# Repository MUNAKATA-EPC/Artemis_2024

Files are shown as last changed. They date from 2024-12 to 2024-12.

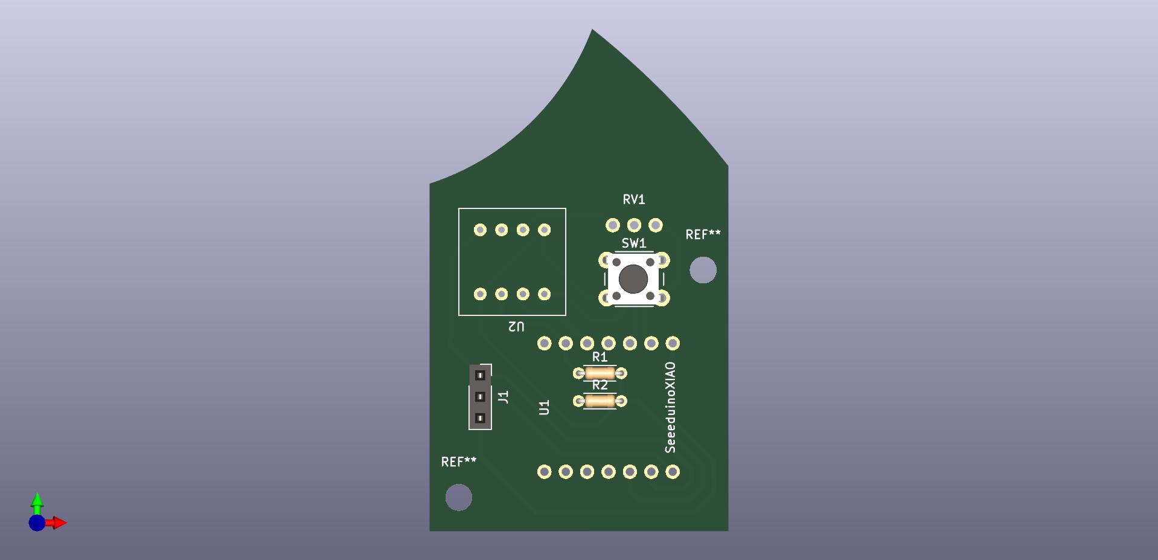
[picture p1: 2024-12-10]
Project_Testing_AkizukiMotor/Hardware/3d_data/gyro_board_texture/gyro_board.jpg

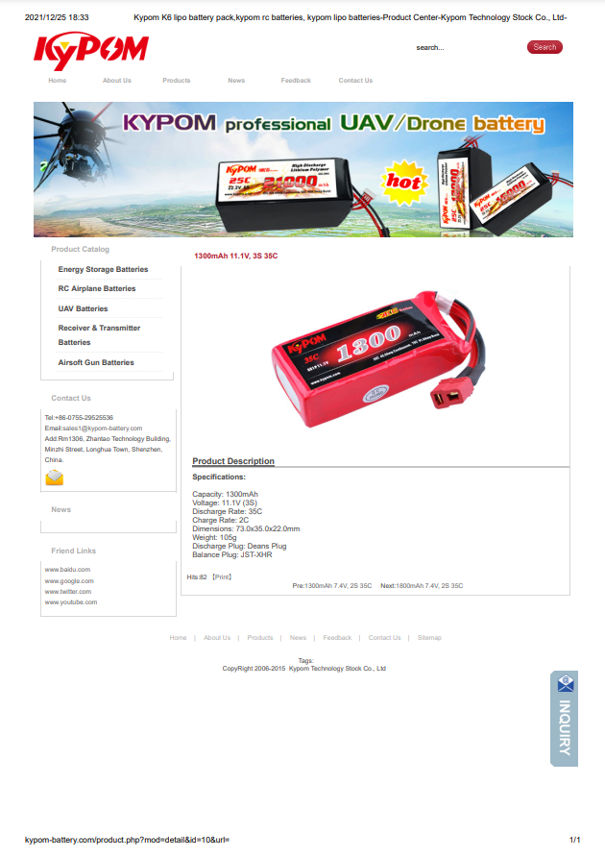
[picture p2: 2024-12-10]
CommonData/Tounaments_Data/2024_04_JapanOpen/battery_document/提出/WSL000_3.png

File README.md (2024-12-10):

# Artemis_2024

宗高アルテミス 2024シーズンリポジトリです。

OpenLeague→LightWeightと方針を転換しました。
OpenLeagueの残骸に関しては2025シーズンに向けての開発と思ってもらえればよきです。

## 最終活動結果
### 北九州ノード 
  優勝  
### 九州ブロック 
  準優勝 / 優秀プレゼンテーション賞  
### RoboCupJunior2024 JapanOpen Nagoya 
  世界大会推薦順位3位  
### RoboCup2024 Eindhoven 
  Individual 3rd Place / Top Poster & Presentation  

## リポジトリについて
・フォルダ階層をきれいにしよう  
・パス設定は相対パス基準にしよう  
・あとは動けばなんでもよし。  

## 命名規則など
・各ロボットごとにプロジェクトファイルを作成しましょう。(英字表記推奨、フォルダ名に2バイト文字は嫌じゃ！！！！)  
　ex. Project_FukuokaNode

・PlatformIO等で作成されたプロジェクトフォルダの名前は (プロジェクト名)-(開発環境) にしましょう。  
　ex. hogehoge-teensy40 hugahuga-seeeduinoxiaorp2040
 
・KiCad、Fusion360などで作成されたフォルダ、ファイルの名前は一目でわかる名前にしましょう。  
　間違ってもファイル名を"unko"とかにするなよ！！！！！(戒め)

 ## 使用ソフト
 |系統|ツール|
 |----|----|
 |ロボット設計|Autodesk Fusion 360  |
 |回路設計|KiCad 6.x (only use 6.x ver.)  |
 |プログラム開発|Microsoft Visual Studio Code <br>Arduino IDE   |

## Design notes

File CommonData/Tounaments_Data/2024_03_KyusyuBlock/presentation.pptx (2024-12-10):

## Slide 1

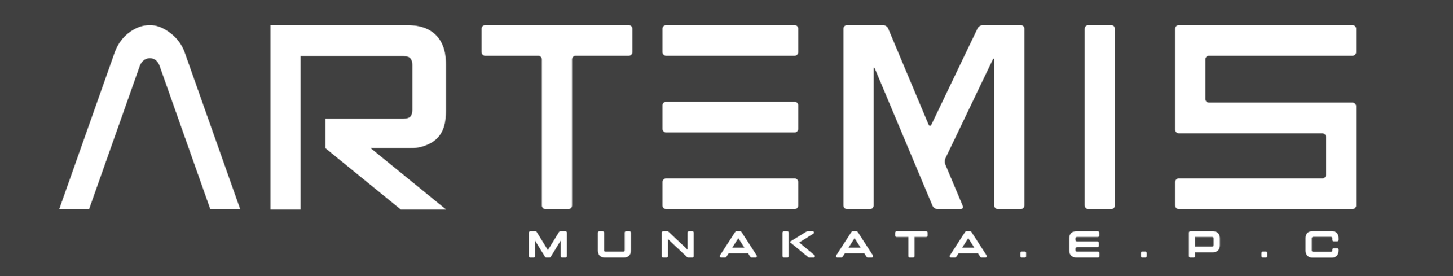
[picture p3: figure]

福岡県立宗像高等学校

チームメンバー

松田 魁琉 / 目野 優輝 / 石原 廉太郎 / 熊抱 崚太

所属ブロック

九州ブロック 北九州ノード

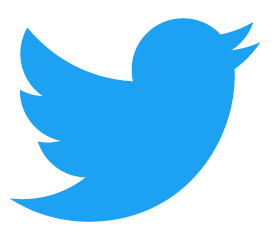
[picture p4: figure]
Twitterロゴのダウンロード方法と利用規約をわかりやすく解説

@munako_artemis

ロボットの概要 – 2024 Season Munako Artemis’ Robot

- 搭載している部品
・バッテリー　　　　:　KyPom 3Cell 1300mA
・モータードライバ　:　DSR-1202
・モーター　　　　　:　IG22 19:1 x 4
→ 応答性の高さから採用しました。
・メインマイコン　　:　Teensy 4.0 x 1
→ シリアル用ピンの多さから採用しました。
・サブマイコン　　　:　Seeeduino Xiao x 3
→ ジャイロセンサ・ラインセンサ・ボールセンサの処理用。
・ボールセンサ　　　:　TSSP58038 x 8
→ ボールから発せられる赤外線を読み取り、サブマイコンで
計算を行ってボールの角度を距離を算出しています。
・ラインセンサ　　　:　S4282-51 x 16
→ 光変調フォトICを使用し、白線の判別をしています。
ベクトルの考えを用いて白線の角度を算出しています。

私たちのロボットでは多くのセンサを円形に配置して使用しています。

カメラ
正確には「カメラに用いる全方位ミラー」が円形となっています。
カメラの上部に円錐状のミラーを設置することで、全方向のコート
の状況を正確に把握することができます。
私たちのチームでは、敵ゴール、自ゴールの二つを色認識で取得し、
三角関数などを用いて角度・距離を算出しています。
これらのデータで、ロボットが敵ゴールを向きながらキックしたり、
自ゴールに戻りキーパーとして動いたりすることが可能になります。
特に敵ゴールを向きながらのシュートは強力で、中立点からのボール
も正確にシュートすることができます。

カメラ
搭載後…

カメラでゴールの角度を計算することで
ゴールに向かってシュートすることができる

何もないと入らないこのシュートも…

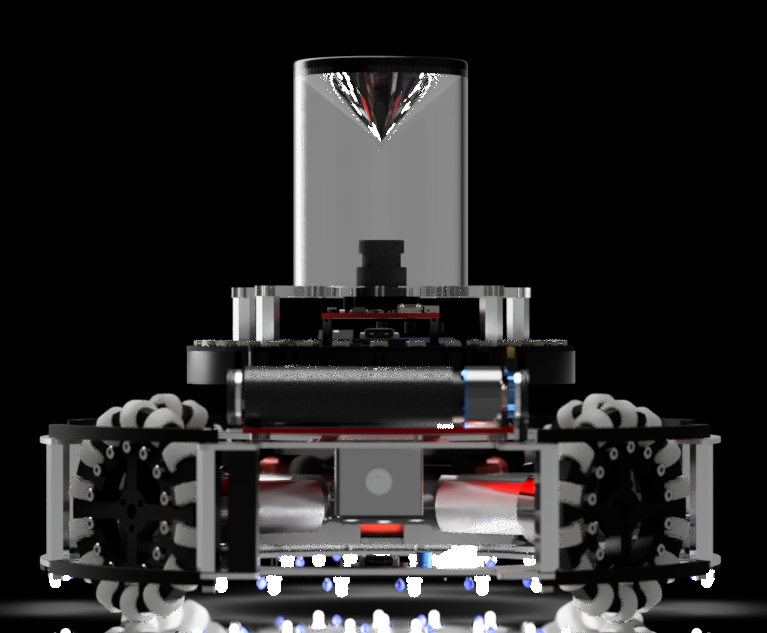
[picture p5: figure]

・ジャイロセンサ　　:　L3GD20H x 1
→ 主にロボットの姿勢を制御するために用いています。
・カメラ　　　　　　:　OpenMV H7 x 1
→ カメラ導入コストの低さから採用しました。
今回の機体では全方位ミラーを用いて360度の方向を監視しています。
・昇圧回路　　　　　:　XL6009
→ ソレノイド駆動電源の生成で使用しています。(12V → 30V)
・ソレノイド　　　　:　CB1037
→ 所謂「キッカー」という機構で用いています。
ボールをキックし推進力を与えることができます。
・ドリブラー用BLDC
→ AliExpressで購入した比較的小さいBLDCです。
ボールを自ロボット側に回転させることでボールを保持します。
主に安定したキックをするために使用しています。

金属製でロボットを強固に

- CNCによる金属加工 -

モーターの変更によりタイヤを強固に
固定する必要がありました。初めは3Dプリンタ
を用いて製作していましたが、部品が折れる
などの問題が頻発したため、OriginalMind社の
CNCを用いることで、時間のかかる金属加工を
自動で行い、タイヤ・タイヤ固定具を強固に、
そして安定させることができました。
(右図：ロボットに取り付けた金属部品)

ドリブルとキックで「魅」せる

- ドリブラーとキッカーの搭載 -

2024シーズンの私たちの新しい取り組みとして、「ドリブラー」「キッカー」の
搭載を行いました。ドリブラーは主にボールの保持、キッカーはボールのキック
という役割を果たします。
キッカー
キッカーの仕様は右図の通りです。
バッテリーからのの11.1Vを昇圧回路で
30Vに昇圧しています。また、
コンデンサへの充電部分、ソレノイド
駆動部分をFETによって分断することで
マイコンへのノイズ対策をしています。
Digital(黄色部分)はメインマイコンに
接続されており、フォトカプラに3.3Vの
電圧をかけることでそれぞれの信号を
出力させています。
キッカーによりゴール前における
プッシング発生率を大幅に減少させる
ことができます。
ドリブラー
ドリブラーにはAliExpressで購入したBLDCを用いています。3Dプリンタで制作した
回転体にゴムチューブを取り付け、それをBLDCを用いて回転させています。
そのままだとドリブラーがボールの高さより上に上がってしまい、ボールをうまく
回転させることができなかったため、回転部分と固定部分にバネの両端を
取り付けました。そうすることによって、
回転部分が回転した時にバネが捻られ、
元に戻そうとする力が働くことで結果的に
ドリブラーがボールをを押さえつける
という機構を実装することができました。
今大会では、ドリブラーを用いて、
ボールをゴールまで運んだり、
キックを安定させるための機構として
使用しています。

円形で全方位を見る

- 円形配置による全方位の監視 -

昇圧回路
12V → 30V

C
4700
μF

+30V

Digital

フォトカプラ

+30V

Pch MOSFET

フォトカプラ

ソレノイド

ボールセンサ
ボールセンサ(TSSP58038)を円形状に8個配置しています。ボールの角度・距離を取得するために、まずは一番反応している
センサーを取得し、次にその周囲3つのセンサーのデータを元に
ベクトル計算を行うことで、360度単位での角度取得が可能になりました。

ラインセンサ
光変調フォトIC(S4282-51)を円形に16個
配置し、2個ずつに分割してサブマイコンで
処理をしています。各センサーの値を見て
白線の角度を算出し、前回の白線の角度と
照らし合わせることで、「ロボットが白線を
踏んでいる」「ロボットが白線を超えた」
という状況を判別することができるように
なりました。

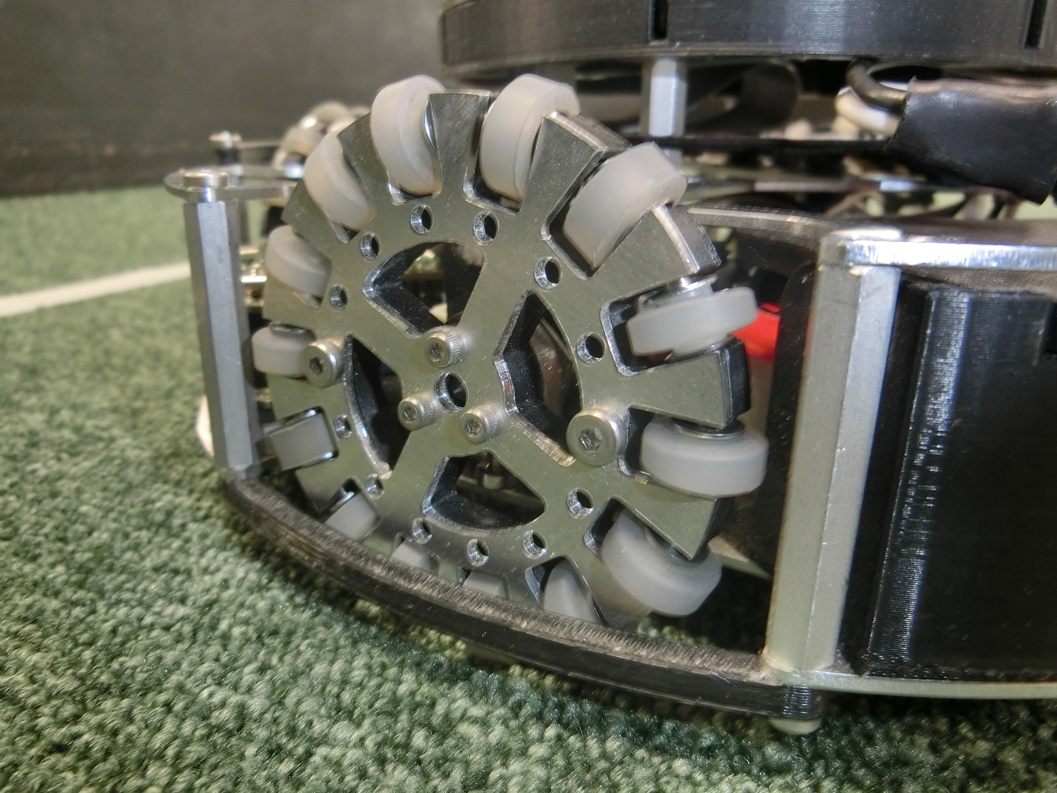
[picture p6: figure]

+30V

Nch MOSFET

+30V

+5V

Digital

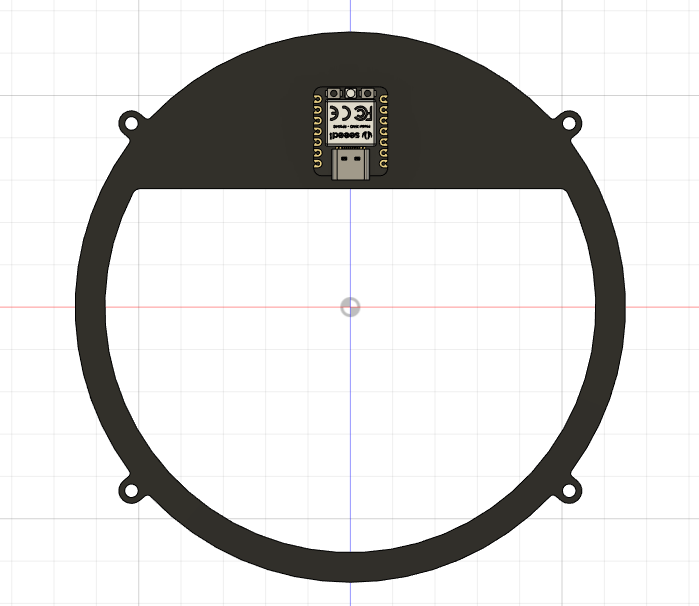
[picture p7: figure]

強いロボットは環境から

- 私たちの開発環境 -

私たちはロボットの開発のために以下のツールを使用しています。
環境を統一して活動することでロボットの開発を円滑に進めることができます。

<ハード>
ロボット設計　： Fusion360
基板設計　　　： KiCad 6.0
<ソフト>
プログラム制作：Visual Studio Code
Arduino IDE

<データ共有>
Githubを用いてチーム内で
リアルタイム共有を行っています。
<コミュニケーション>
Discord、Asanaを用いてタスクや進捗をチーム内で共有しています。

スポンサー

+30V

昨年度から白線外の空間が縮小し、白線外に出ないような
工夫が必要になりました。すべての速度を落とすという対策も
ありますが、これだと全体的なスピードを失うことになります。
そこで、ロボットの移動する角度を縦、横に分解し、その方向に
どのくらいの時間移動したかをタイマーで取得することで、
速度の変化の割合を変化させるという処理を実装しました。
これによって、コート内では素早く動き、白線付近では比較的
スローな移動にすることができました。

白線外など言語道断

- プログラムによる速度調節 -

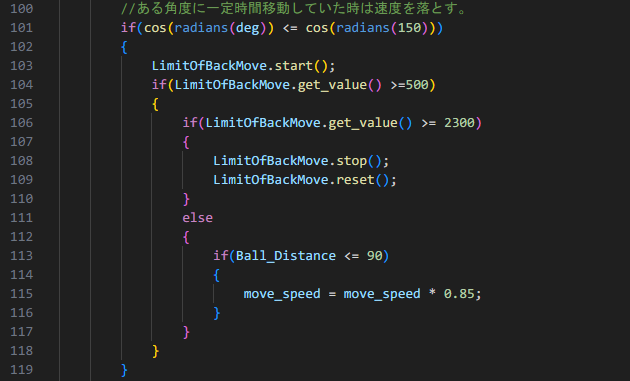
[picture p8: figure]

実際のプログラム
LimitOfBackMove というタイマー変数によってある方向に対する移動時間
の検知を行い、速度の割合を減少させている(115行目)。

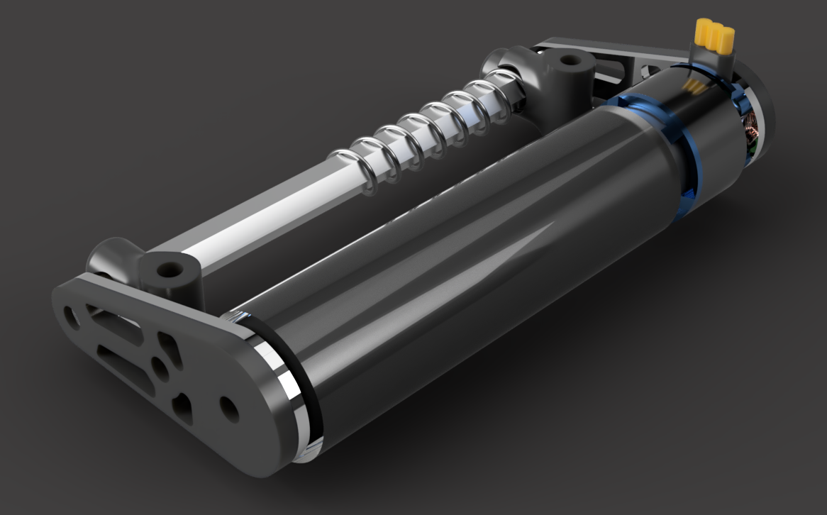
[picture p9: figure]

私たちが制作するロボットにはJLCPCB様の基板を使用しています。
JLCPCB様にスポンサーになっていただき、格安で基板製造をしていただいて
おります。また、JLCPCB様とのタイアップ記事も制作しているのでぜひ
JLCPCB及び私たちのウェブサイトをご覧ください。

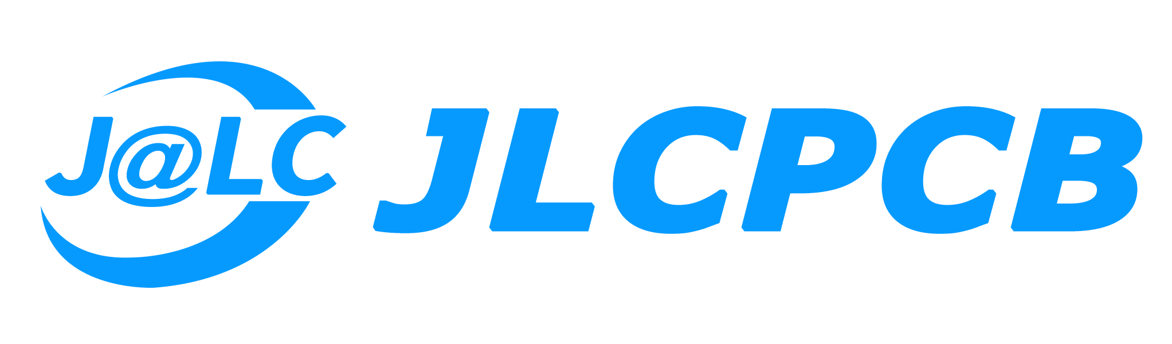
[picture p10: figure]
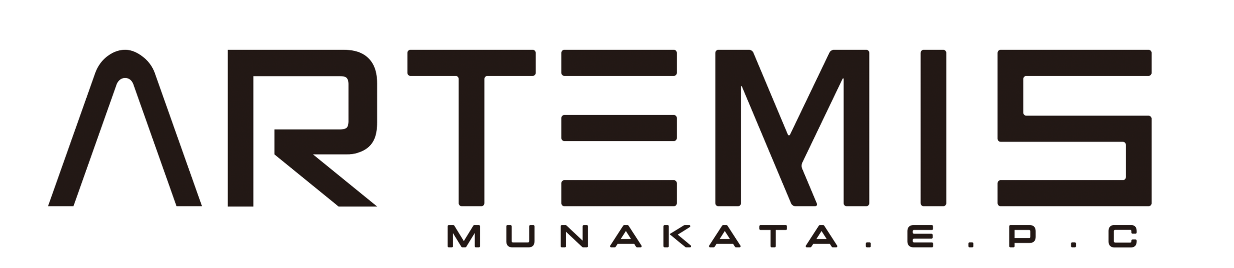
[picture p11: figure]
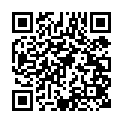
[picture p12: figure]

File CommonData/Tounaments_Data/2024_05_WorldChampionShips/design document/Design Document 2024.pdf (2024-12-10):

# Design Document 2024 Munako Artemis

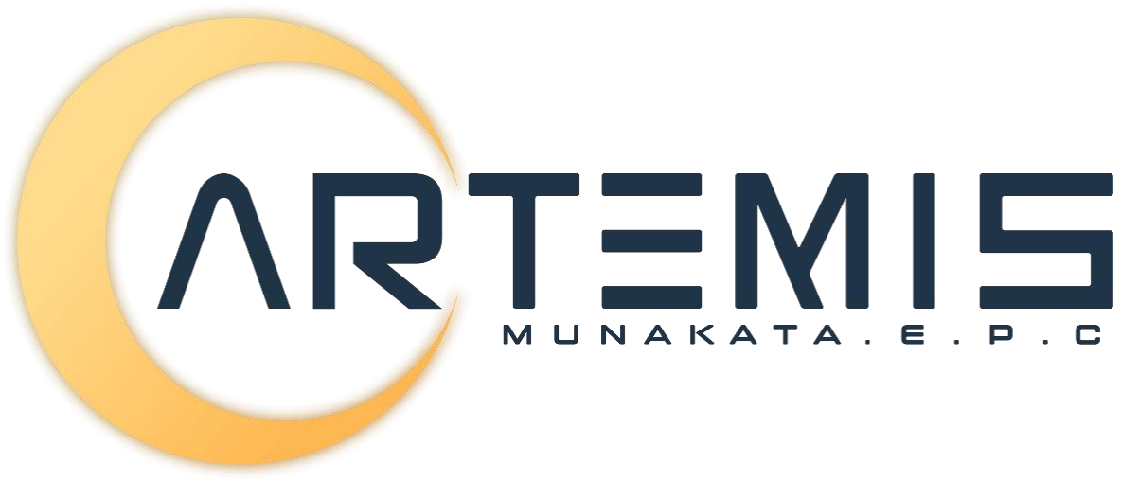
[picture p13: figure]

Munakata High School Electric Physics Club Region: Japan
League: Soccer Light Weight
Team member: Kyle Matsuda, Yuki Meno, Rentaro Ishihara, Ryota Kumadaki Team HP: https://munako-artemis.github.io/

### Team Introduction:

Munako Artemis is a Japanese team participating in Soccer LWL. The team consists of four high school students and has been active since 2021.

### Members:

・Kyle Matsuda | : Robot 1 Hardware (Robot design, Circuit design)
・Yuki Meno | : Robot 2 Hardware (Robot design, machining)
・Rentaro Ishihara: Robot 1 Software, Team management (Low layer programing) ・Ryota Kumadaki: Robot 2 Software (Main program)

### Abstract

| This year, we developed two types of robots. The robot in the
| left of fig.1 is designed to have a low center of gravity and high
| maintenance performance. The right one is designed to be a
| strong robot with stable operation. In the developments of
| these two robots, we made modifications to our robots to
| address various issues identified in the Japan Open 2024.
| We were given an extremely short preparation period for the
| world championship, so we proceeded with multiple workflows,
| which not only allowed us to start working on tasks earlier but
| also created significant time flexibility.

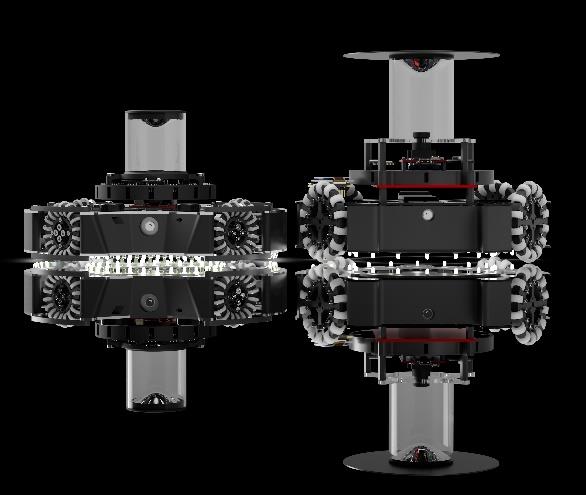
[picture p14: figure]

Fig.1 (robots for the world championship)

### Team Management

Our team is primarily divided into hardware and software teams. As a result, it was often difficult to understand the status of each team during actual activities. Additionally, the time available for work was limited due to the short period until the competition. Therefore, we made significant improvements in two main areas regarding our team activities.

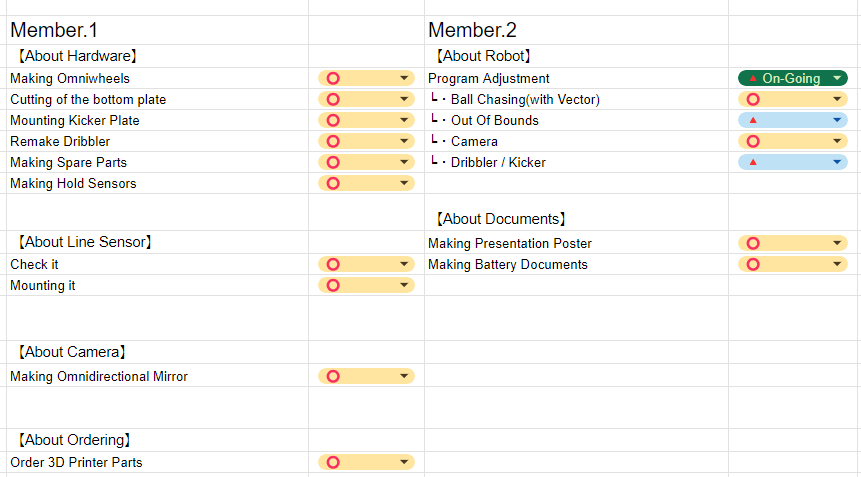
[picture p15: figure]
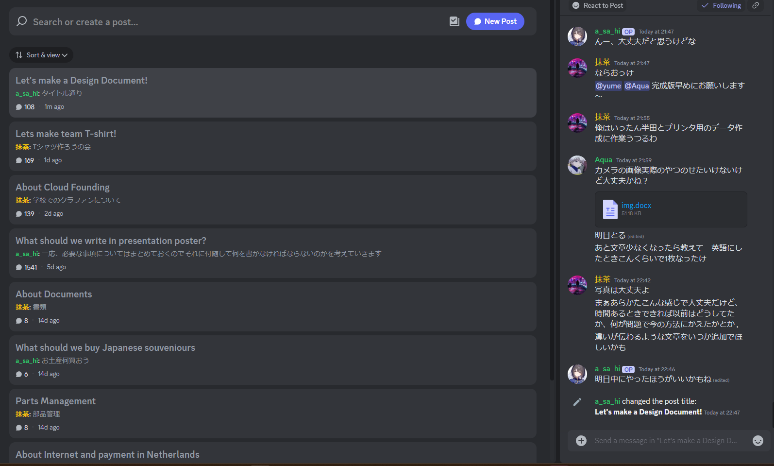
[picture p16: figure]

Fig.2 Task Management Tool (Google Spreadsheet) | Fig.3 Communication Tool (Discord)

<Task Visualization and Smooth Communication>
To visualize tasks, we used Google Spreadsheet. With Google Spreadsheet, we list and manage each team member's tasks (Fig.2). Since it can be used online, tasks can be checked at any time. Any team

member can add, delete, or edit tasks on the list, making it easy to reassign tasks to other team members if any issues arise. This allows the entire team to stay updated. This tool made task visualization clear and facilitated smooth team activities.
For smooth communication, we used Discord. Discord was primarily used for discussions related to team activities (Fig.3). By using the Discussion function, we could create channels for each topic,

enabling smooth discussions on specific topics.

<Workflow Improvement>
We had a short preparation period leading up to the world championship, necessitating efficient work processes. To address this, we focused on "improving our workflow."

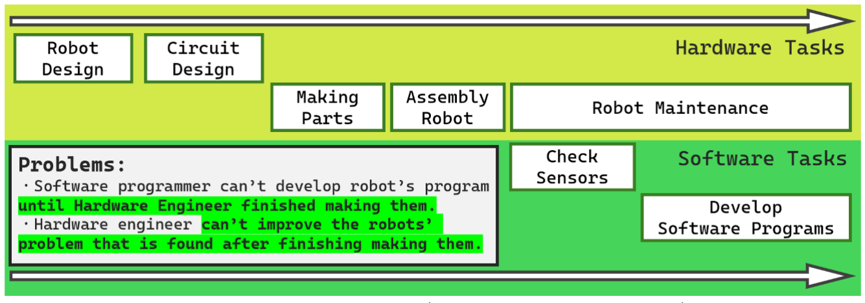
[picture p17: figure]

Fig.4 Single Workflow System (From Our Presentation Poster)

Previously, as shown in Fig.4, we followed a workflow system where tasks were completed one at a time. This method ensured more reliable results, but it takes longer to process tasks sequentially. As a result, it made it difficult to provide feedback from software development issues to the hardware team

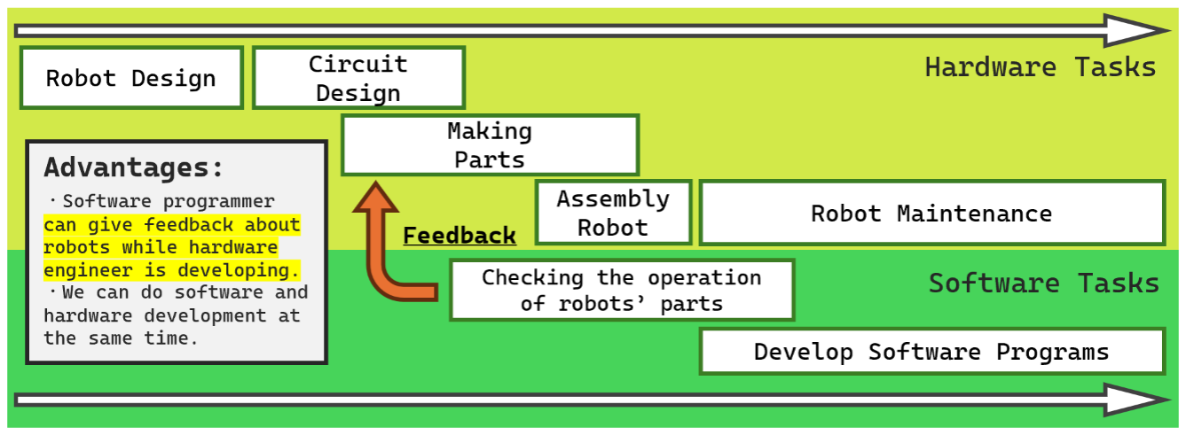
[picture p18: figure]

F ig.5 Multiple Workflow System (From Our Presentation Poster)

Therefore, we adopted a multitasking flow, as depicted in Fig.5, where team members work on multiple tasks in parallel. By working on tasks simultaneously, we enabled feedback from software to hardware, allowed system changes during the design phase, and confirmed the operation of each component before the robot's completion. This approach facilitated smoother program adjustments for the robot post-completion. By implementing these improvements in team activities, we were able to develop the robot smoothly and facilitate efficient team collaboration within a short period.

### Robot Specifics

<Robots’ Overview>

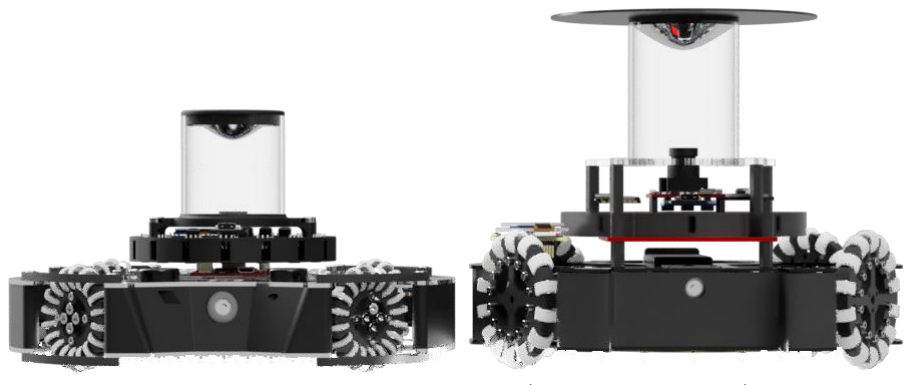
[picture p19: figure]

Fig.6 robots for the world championship (left: robot1 right: robot2)

Robot.1's concept is to be a "robot with a low center of gravity and high maintenance performance”. Also, it has been designed with a reduced number of components, ensuring ease of maintenance despite its low-profile design. Robot.2's concept is to be a "strong robot with stable operation". Additionally, it is designed to place various additional components for adapting to changes in rules.

<Robot1 Mechanical>
・low center of gravity

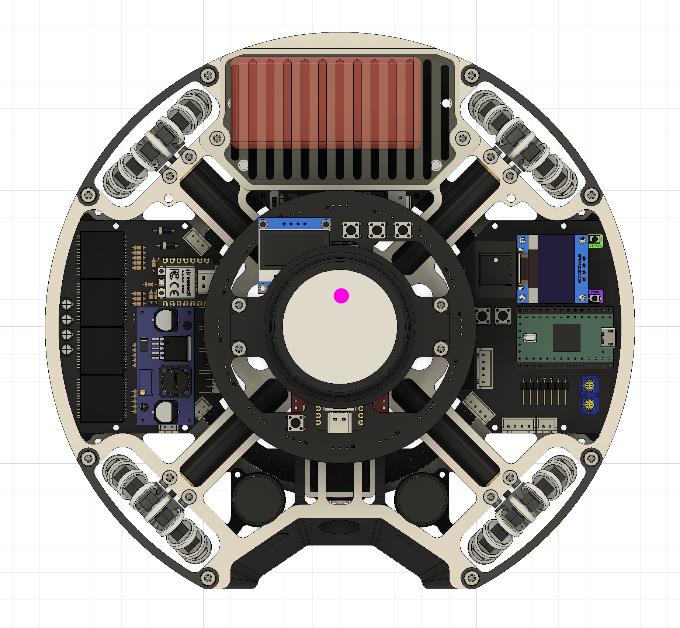
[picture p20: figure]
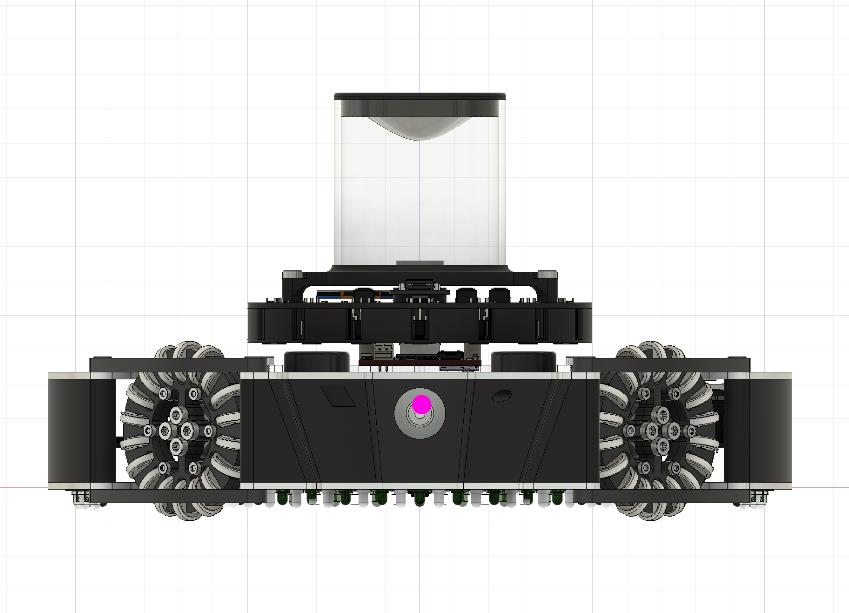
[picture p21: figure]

Fig.7 The position of the center of gravity of Robot 1.

This robot prioritizes a low center of gravity.
The pink dots shown in Fig.7 indicate the robot's center of gravity.
A low center of gravity allows the robot to execute turns and speed changes with minimal force, reducing power consumption and enabling more precise movements.
However, achieving a low center of gravity often means designing the robot to be compact and
densely packed with components internally, potentially compromising maintenance accessibility. To address this problem, we made various improvements shown on the next page to this robot.

・maintenance performance

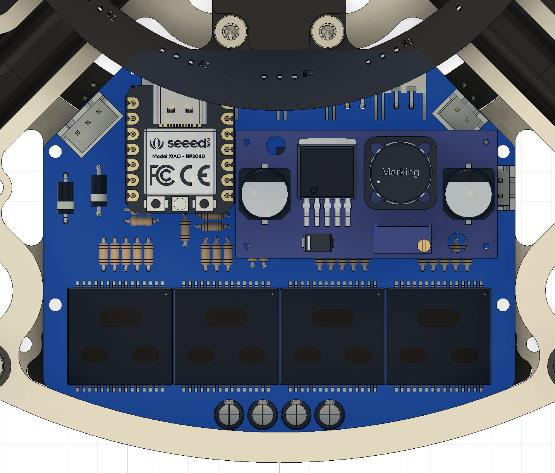
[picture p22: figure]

Fig.8 The shapes and location of some of the biggest boards in the robots. (Boards are colored in blue)

As mentioned earlier, low profile robots mean designing the robot to be densely packed with components internally, potentially compromising maintenance accessibility. Therefore, we paid special attention to the location and shape of the circuit boards. As shown in Fig.8, larger boards are especially placed in areas without obstacles, and designed to be secured with no more than four screws. Regarding the shape, instead of forming boards that fit tightly along the frame and surrounding components, we adopted simple shapes that do not interfere with other parts during removal.

・Improving the Shape of the Omni-Wheel

To achieve more stable and efficient movement, we changed the shape of the omni-wheel.

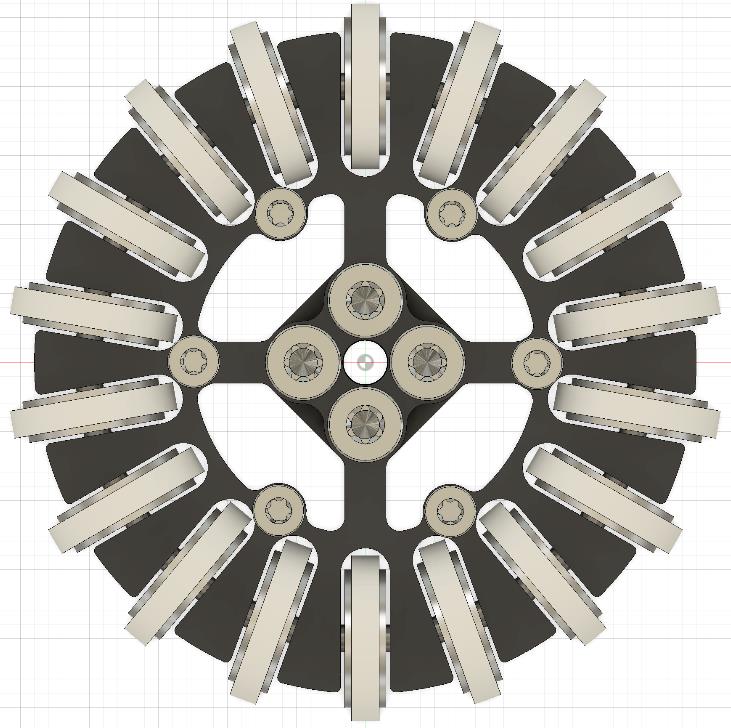
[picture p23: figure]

Fig.9 The old and new omni wheel

Previously, as shown in the left of Fig.9, we used omni-wheels with thick side wheels. However, starting from the 2023 Japan Open, we switched to a design with thin side wheels, as shown in the right of the Fig.9.

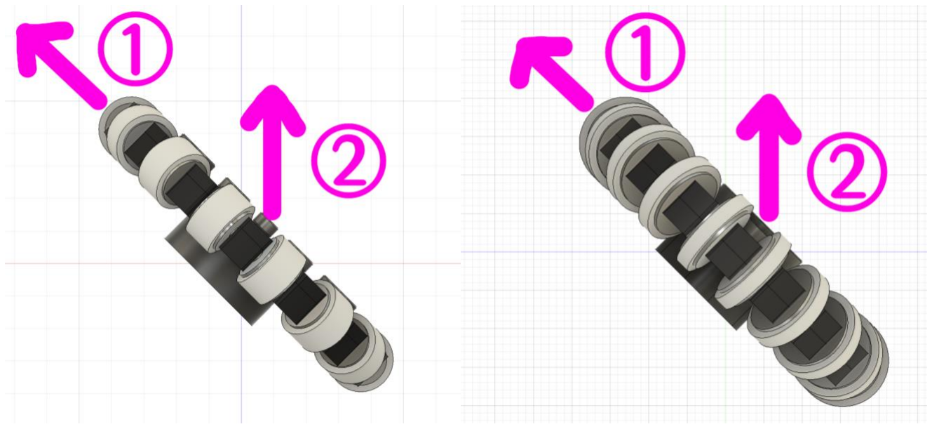
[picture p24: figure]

Fig.10

In the previous design, moving in direction →① was not a problem, but when moving in direction →②, the large contact area with the ground required more force due to increased friction. In the

current design, the thin side wheels reduce the contact area with the ground, resulting in less friction and allowing for easier movement with less force. Additionally, the difference in the amount of force needed depending on the direction is minimized, leading to less speed variation and more stable robot movement.

<Robot2 Mechanical>
・Designing

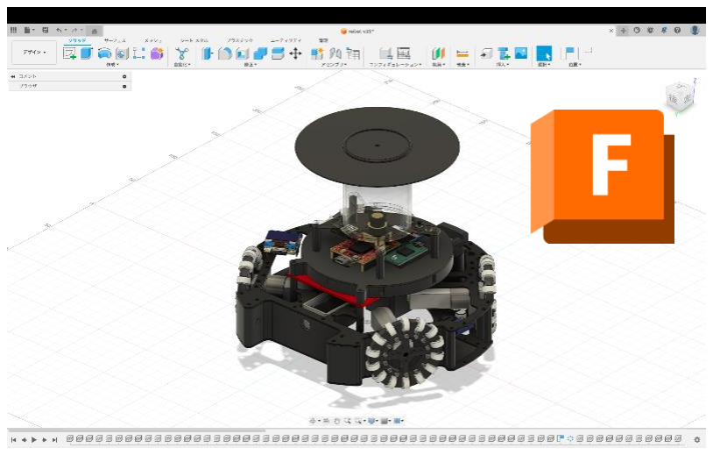
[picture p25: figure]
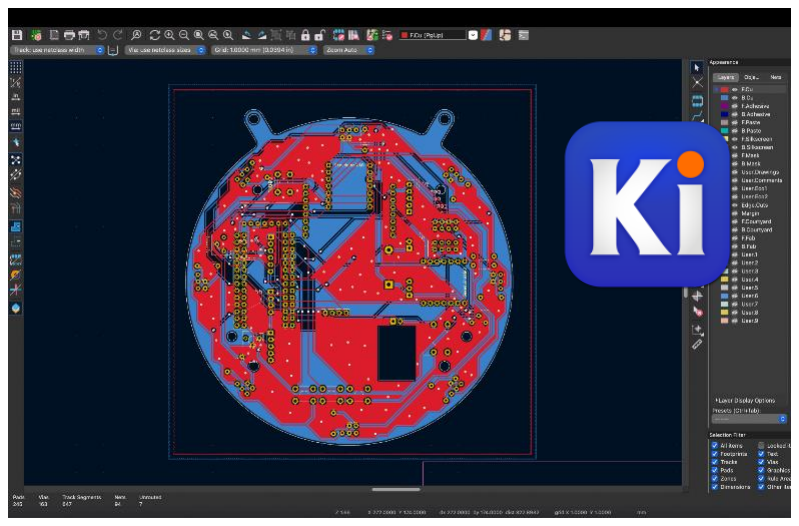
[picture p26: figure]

Fig.11 | Fig.12

We use Autodesk Fusion for the design of Robot 2 and KiCad 6.0 for the circuit design. By using these software tools, we have been able to develop a high-performance robot.

・Expansion Of The Ball Capture Zone

The robots we developed and produced up until the Japan Open 2023 had a narrow ball capture area, making it difficult to move the ball forward effectively and capture it smoothly during matches. (fig.13)

For the robots developed for the world competition, we have expanded the ball capture area compared to the previous robots. (fig.14) This expansion has resolved the issues faced by the earlier robots,

significantly improving the ball capture rate.


fig.13 | fig.14

・Improvement Of The Line Sensor

Until the Japan Open 2024, our robots were equipped with only circular line sensors. However, with only the circular line sensors, it was challenging to fully detect the white lines, leading to frequent out-of-bounds occurrence.
This time, as shown in the figure, we added side line sensors in addition to the circular ones.
This addition has significantly reduced the out-of-bounds rate compared to before.

・Motor Specifications

We use the DIGILENT IG22 1/19 motor. This motor is lightweight and compact yet offers high responsiveness and speed, which is why we chose it. Previously, we used motors with high torque and high rotation speed but lacked responsiveness, making posture control and sudden direction changes difficult, and programming the robot was extremely challenging. From this iteration, we have started using motors that combine high responsiveness.

・Solenoid Specifications

We use the TAKAHA solenoid for the kicker.
Specifically, we have chosen the CB1037 push solenoid from TAKAHA, which has a long stroke and delivers high output despite its small size. The kicker circuit is explained in detail on the next page under the section <Electric Circuits>.


### <Electric Circuits>

Our robots consist of two types, but we try to use the same circuits as much as possible to quickly determine the cause in the event of a failure and to make parts redundant.
In this document, we wrote about our power supply circuit and kicker circuit.

・Power Supply Circuit


Fig.15 (circuit of the power supply) | fig.16 (the circuit board)

The power circuit board includes a battery protection, and circuits for generating both the drive power supply and control power supply. The battery protection circuit is equipped with a reverse connection, overcurrent, and over-discharge prevention. To generate the control power supply, a DC-DC converter is used. By using a DCDC converter, electrical noise caused by motors and voltage drops due to the use of a kicker can be blocked, and a constant, stable power supply for control can always be provided. This ensures stable operation of the robot without resetting the microcontroller or sensors, even when equipped with high power motors or power-consuming dribbler mechanisms.

・Kicker Circuit


Fig.17 (circuit of the kicker circuit while charging) Fig.18 (circuit of the kicker circuit while kicking)

Previously, we did not implement noise countermeasures, resulting in voltage drops and unstable supply to the control power. This time, we have made numerous improvements to the kicker circuit to minimize noise as much as possible.
Firstly, to prevent noise from directly affecting the microcontroller, we have introduced a photocoupler into the signal lines. Secondly, we use separate FETs for solenoid control and isolate the kicker circuit from all other circuits only at the moment of the kick. This approach not only prevents noise from directly reaching the control circuits but also eliminates noise transmission through the power supply, leading to a much more reliable kicker circuit.

### <Robot1’s Software>

・Processing of the Defense Program


Fig.19 Defender System

Robot.1 primarily serves as a defender. The defense system is implemented using two types of sensors: a circular line sensor and a ball sensor. The robot stays on the goal line and moves or stops based on the ball's angle of response. Fig.19 illustrates the defense system, where the large translucent circle represents the robot, and the smaller red and white circles within it represent the line sensors.
In Fig.19 (①), when the ball is detected within ±15° of the perpendicular angle formed by the line connecting the active line sensors, the robot stops. In Fig.19 (②), when the ball is detected beyond ±15° of the perpendicular angle, the robot moves in the direction indicated by the line sensor's angle towards the ball. Previously, the robot only moved in the direction of the ball while on the white line, which caused inefficiencies in returning to the goal line. By adjusting the movement direction based on the line sensor's response angle, the system now achieves two objectives simultaneously: staying on the goal line and moving towards the ball. This improvement allows for smoother movements and more effectively blocks the opponent's shots on goal.

・Line Sensor Algorithm


Fig.20 An algorithm of Circle Shape Line Sensor

Like Robot.2, Robot1 is equipped with a circular line sensor. By using a circular line sensor, the robot can accurately detect how it is crossing the white line, significantly improving the accuracy of out-of-bounds prevention.Fig.20 illustrates the algorithm of the sensor. In the figure, the right side of the white lines represents the inside of the court, while the left side represents the out-of-bounds zone. In cases ① and ②, the robot moves in the direction opposite to the sensors that detect the white line. In case ③, the detected direction would normally cause the robot to move towards the out-of-bounds

zone. However, by comparing the current angle of detection with the previous one, if there is a significant change, the robot recognizes that it has crossed more than halfway over the line. It then moves in the opposite direction to avoid going out of bounds. This way, the circular line sensor ensures the robot calculates the correct direction to move, even if it has crossed the line by more than half.

### <Robot2’s Software>

・Color tracking using a camera


Fig.21 360 view ＆ robot movement

Fig.21 shows an example of color tracking using OpenMV. By using an omni directional mirror, it is possible to see the entire court area at 360 degrees. In this example, thresholds for the colors of the goal and court are set as arc tangents, calculating angles and distances from the camera center simultaneously. The calculated angles and distances are transmitted via UART to the main microcontroller. Using the angles, the deviation between the goal's center direction and the robot is calculated, enabling PID control to orient towards the goal direction. This approach improves goal alignment rates compared to using only a gyro sensor. However, issues arose due to variations in lighting affecting how the goal appears. To address this, adjustments were made to the gamma value, contrast, and brightness of the images obtained from the camera, allowing the robot to adapt the visibility of the goal based on the current environment.
Regarding the Attacker mechanism, previously, the robot would orient towards the goal direction when the goal was visible and towards the front direction using the gyro sensor when the goal was not visible. However, a problem was identified at the national tournament where the visibility of the goal frequently alternated at the boundary of visibility, disrupting smooth movement as the direction control switched between gyro direction and goal direction. Therefore, a new approach was implemented where the robot faces the goal direction when holding the ball or when near the goal (as shown in Fig21). This change prevents frequent switching between goal and gyro directions, leading to an improved goal alignment rate.

### <Review ＆ Future Goals>

Our final goal is to achieve victory in both the Lightweight League and the Open League.
Reflecting on this season, we aim to develop an even better robot for the upcoming season based on the following lessons learned:
Improvements in Design: We aim to enhance performance by continuing to lighten the robot and strengthen its structure. Optimizing component placement and design shapes will further improve maintenance and durability.
Sensor and Control Systems: We plan to refine the accuracy and reliability of color tracking using cameras.
Enhancing Stability and Accuracy of Operations: Prioritizing responsiveness in gyro sensors and motors will enhance operational stability. Optimizing software algorithms will ensure flexibility in handling unforeseen situations.
Refinement of Competitive Strategies: Further refining the roles of attackers and defenders will allow for more strategic gameplay. We will consider additional features to support strategic play.
Team Coordination and Communication: Enhancing the use of project management tools will streamline team progress tracking and issue resolution. Improving communication among team members will foster better collaboration.
We are committed to developing a robot that is more advanced and competitive, building on the challenges and successes of this season.

### <URL>

・Our team HP: https://munako-artemis.github.io/・GitHub: https://github.com/MUNAKATA-EPC/ (https://github.com/MUNAKATA-EPC/Artemis_2023) ・Contact us: kyle.matsuda.0518@gmail.com

This document only covers a part of our robot.
If you have any other questions or concerns, please contact us.

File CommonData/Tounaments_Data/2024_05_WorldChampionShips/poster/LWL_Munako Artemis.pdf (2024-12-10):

# Robo.1

# Munako Artemis

# Munakata High School

# REGION

JAPAN | Soccer LWL

# LEAGUE

## Team Website

### https://munako-artemis.github.io/

## Team X(Twitter)

### https://x.com/munako_artemis

## Team GitHub

https://github.com/MUNAKATA-EPC | Website X(Twitter) | GitHub

# Team Member

Kyle Matsuda | : Hardware
Yuki Meno | : Hardware

## Rentaro Ishihara : Software Ryota Kumadaki : Software

### Munako Artemis is a Japanese team participating in Soccer LWL. The team consists of four

high school students and has been active since 2021.

For robot design, we mainly use Autodesk Fusion, and for circuit design, we use KiCad. By utilizing 3D printers and CNC milling machines, we efficiently created our robots. Almost all the sensors and microcontrollers are the same among both of our robots,

### simplifying parts management and increasing compatibility. Additionally, the programming

is primarily done in C+/ for most microcontrollers and in MicroPython for the camera.

In preparation for the world tournament, we made modifications to our robots to address various issues identified in the Japan Open 2024. One significant problem was the frequent occurrence of out-of-bounds, so we improved the shape of the line sensors from a linear to a circular design and changed the sensor processing algorithm. Additionally, we often had difficulty carrying the ball forward, so we expanded the ball-capturing zone to

make it easier to capture the ball and improved the ball-tracking algorithm.

Both of our robots are equipped with a kicker mechanism that uses a solenoid to kick the ball. However, we had no idea which voltage and capacitor capacity would result in the strongest kick. Therefore, we investigated how the kicking power changes with different voltages and capacitor capacities and created graphs to determine the optimal settings

for the strongest kick.

### Although this is our first time participating in a world tournament, we are strongly motivated by the desire to "interact with various people, acquire diverse knowledge, and gain valuable experiences." To share our knowledge with a wider audience, we have created

a website and social media accounts.

Robo.2 | Battery Kypom 3S 11.1V 1300mAh

### Motor

DIGILENT IG22 1/19

X 4

11.1V

11.1V

Motor Driver
DAISEN DSR-1202

IC:VNH2SP30 x 4
・0.3V ~ 16.0V
・15~30A / channel

11.1V

Voltage
Conversion Circuit

Using IC :
OKL-T/6-W12N-C
11.1V to 5.0V
5.0V
UART | ANALOG

11.1V

About
48V

### Kicker System

(Please look at
“Kicker System And
Research About
Voltage & Capacity Of
Capacitors”)

### Solenoid

CB1037 x 1

UART
I²C + Digital x 3

Debug System

O-LED
Display
SSD1306 x 1

Tactile Switch x 3
( For switching
robot’s mode)

I²C

UART

# Abstract

## 【About the kicking mechanism and the research about the voltage and the capacitance of capacitors】

Our robots are equipped with a solenoid which is used for a ball kicking mechanism. It can kick the ball when you apply high voltage to the solenoid and uses a big capacitance charging capacitor.
The circuit of the kicker mechanism is shown below Fig.1.

However, we had no idea how high the voltage and how big the capacitance of the capacitor should be when we use the solenoid as the kicking system.
Therefore, we decided to research how the kick power will change when we changed the voltage and capacitor capacitance.

## <Details Of Research>

Measure the difference of the kicking power when you changed the voltage applied to the solenoid and the capacitance of the capacitor to find the optimal conditions for equipping the solenoid on the robot.
This time we used capacitors from NIPPON CHEMI-CON, Nichicon, Rubycon.

## <Research Procedure>

Step 1. make a solenoid drive board which can change the charging capacitor and the voltage which will be applied to the capacitor.
Step 2. Measure the kick power (/1) by keeping the voltage constant and varying the capacitance of the capacitor.
Step 3. Measure the kick power (/1) by varying the voltage without changing the capacitance.
Step 4. Create a graph based on the experimental data obtained from Step 2 and 3.

(/1) Place a long ruler on the court and kick the ball on it and the kicking power is defined as the distance the ball stopped.

## <Results>

In Fig.2, you can see that the voltage variation and the change in kicking power follow a linear relationship. Similarly, in Fig.3, the change in capacitor capacity and the variation in kicking power also appear to follow a linear relationship.

## <Discussion>

Based on these findings, it is considered that higher voltage and larger capacitor capacity lead to greater kicking power. Therefore, we aimed to get as close as possible to the maximum voltage limit allowed by the rules, which is 48V, and selected capacitor capacities based on the available space inside the robot. Robo.1 was equipped with a ?/μF capacitor, and Robo.2 with two 4700μF capacitor, to maximize kicking power as much as possible.

# Our Robots’ Structure

# Method / Production / Design

# Data / Results / Discussion

Sub Controller

Seeeduino Xiao

Sub Controller

Seeeduino Xiao

# Team Activities

## 【Enhancing Team Collaboration with Various Tools】

### In our team, we make our collaboration in diverse aspects such as robot design and programming more efficient by using a variety of

tools.

### All the tools we use are shown below:

### ・Robot Design : Autodesk Fusion ・Circuit Design : KiCad 6.0 / 7.0

### ・Programming Tool : Visual Studio Code

### ・Source Management : GitHub

### ・Communication Tool : Discord

### ・Task Management : Google Spreadsheets

We have set up a team-specific server.
Threads are created for each content area to discuss various aspects in preparation for the world championship, making it easy to understand topics and discussions. (fig.5)
This allows team members to communicate smoothly online, leading to improved robotics
development. Fig.5 Our Discord Server

Fig.6 Task Lists
(From RCJ2024 JapanOpen)

We made a table summarizing tasks for each member. (Fig.6) By managing them online, all team members can add, delete, or edit tasks, simplifying task management within the team. Therefore, at any time, it's easy to understand who has what tasks and the current status of their progress.

## 【Enhancing Team Efficiency through Multiple Workflows】

In team development, the robot production and the software development is difficult to progress at the same time, and this often leads to a single workflow (Fig.7). Given the extremely short preparation period for the world championship, our team found that operating under a single workflow was highly inefficient. Therefore, we proceeded with multiple workflows (Fig.8), which not only allowed us to start working on tasks earlier but also created significant time flexibility.

Robot
Design

Circuit
Design
Making
Parts

Assembly
Robot

To achieve multiple workflows, as we mentioned earlier, we actively used task management tools and communication tools. This allowed the entire team to work on multiple tasks at the same time, thereby enhancing the efficiency of team activities.

### Hardware Tasks

Check
Sensors

Robot Maintenance

Develop
Software Programs

### Software Tasks

Fig.7 Specific System and Problems of Single Workflow

Fig.8 Specific System and Advantages of Multiple Workflow

### Hardware Tasks Robot Design

Circuit
Design
Making
Parts

Checking the operation
of robots’ parts

Assembly
Robot

Develop Software Programs

Feedback

Robot Maintenance

### Software Tasks

### Problems:

・Software programmer can’t develop robot’s program until Hardware Engineer finished making them. ・Hardware engineer can’t improve the robots’ problem that is found after finishing making them.

### Advantages:

・Software programmer
can give feedback about
robots while hardware
engineer is developing.
・We can do software and
hardware development at
the same time.

### Battery

Kypom 3S 11.1V
1300mAh

# 【Robots’ Features】

Gyro Sensors

L3GD20H
&
BNO055

### Vision System

Omnidirectional
Mirror OpenMV H7 x 1

11.1V Voltage Conversion
Circuit

Using IC :
OKL-T/6-W12N-C
11.1V to 5.0V
5.0V

11.1V

11.1V

### Motor

Maxon RE16

X 4

UART

DIGITAL

Sub Controller

Seeeduino Xiao

Line Sensors

S4282-51 x 22

IR Sensors

TSSP58038 x 16

UART

ANALOG

IR Sensors

TSSP58038 x 16

Sub Controller

Seeeduino Xiao
UART
ANALOG

Sub Controller

Seeeduino Xiao

I²C

Gyro Sensor

BNO055

Line Sensors

NJL7502L x 53

UART

### Vision System

Omnidirectional
Mirror OpenMV H7 x 1

I²C
Digital x 3

Debug System

O-LED
Display
SSD1306 x 1

Tactile Switch x 3
( For switching
robot’s mode)

### Main Controller

Teensy 4.0

Wireless
Communication

Twelite UART

Wireless
Communication

Twelite UART

### Main Controller

Teensy 4.0

### Solenoid

CB1037 x 1

### About 48V

Drive Circuit Board : Kicker System And Motor Driver

Sub Controller

RP2040 ZERO

Kicker System

(Please look at
“Kicker System And
Research About
Voltage & Capacity Of
Capacitors”)

Motor Driver

ｘ4
IC : VNH5019A-E

## 1 Omnidirectional vision system

We have positioned the camera facing upwards and placed an omnidirectional mirror at the top of an acrylic pipe.
By doing this, we can capture a 360-degree view from the robot without using multiple cameras, significantly simplifying control compared to using multiple cameras.
We are using OpenMV as camera module. It is programmed with MicroPython. It can be done color tracking easily and easy to handle.

## C. Main Board (Robot.2)

This board is equipped with a Teensy 4.0 as the main microcontroller, an L3GD20H and a BNO055 as IMU sensors, an OpenMV camera, an SSD1306 display, and TSSP58038 sensors for ball detection.
There are eight ir sensors installed to calculate the ball's angle using vector processing.
Two gyro sensors are installed to ensure redundancy in case one fails during the match.
Additionally, the display allows us to check the sensor values and to change the robot's mode without connecting it to a computer, making adjustments to the robot more easily.

## D. Motor Driver : DAISEN DSR-1202 (Robot.2)

We have adopted the DSR-1202 from the Japanese manufacturer DAISEN. It supports high current and can be easily used by connecting to the microcontroller via UART.

## E. Kicker Board (Robot.2)

We use the XL6009 voltage boost IC to step up the voltage to approximately 47V.
For noise reduction, during kicking, we utilize a P channel MOSFET to isolate the kicker circuit from all other circuits, effectively suppressing noise.
The circuit is equipped with two 50V 4700μF charging capacitors. ( For details, check the [ Data / Results / Discussion ] section )

## > Improvement of Ball Access Time through Ball Tracking Algorithm Enhancement

During the national competition, we identified the following issues with our ball tracking algorithm: Lack of distance-based control between the robot and the ball resulted in excessive rounding, leading to delayed ball access.

To address these issues, we developed the following ball tracking algorithm:

In the diagram on the right, we define Ball Angle as the angle of the ball relative to the robot, and Move Direction as the actual angle of movement of the robot.

A. When the robot is close to the ball (Fig.B-1)
Move in the tangential direction to the ball (= Ball Angle + 90) to approach the ball.
B. When the robot is far from the ball (Fig.B-2)
Add a constant (= Ball Angle + X) to move towards the ball.

By doing these, the robot can approach to it shorter way than before, and colliding with the ball is almost nothing, so own-goal was decreasing.

## - Improvement of the shape of the Line Sensor

During the Japan Open 2024, we identified the following issues with our line sensors:

・The sensors were located in the center of the robot.
→ It takes time for the sensors to detect the white line after the robot has crossed it.
・We can only control whether the entire sensor array has detected the line or not,
limiting our ability to implement out-of-bounds prevention measures effectively.
・Poor color compatibility between the sensors and the white line leads to erroneous detections.

To address these issues, we implemented the following improvements.

・Changing the type of the Sensor
Until now, we have been using a sensor called S4282-51. (Refer to the “Touch Sensor” diagram on the left for details.) Although it is resistant to external light, we encountered the issues mentioned earlier. Therefore, we have equipped one of the robot with a phototransistor (NJL7502S).
By changing the sensor, we can sufficiently detect the difference in response between white and green, enabling us to detect white lines and reduce occurrences of out-of-bounds. Additionally, we can adjust the threshold of response circuitry, allowing for more accurate detection of white lines.
(We decided to continue using the S4282-51 in the other robot to ensure redundancy in case the new line sensor encounters difficulties.)

・Changing the shape of the line sensor (Fig.A)
We added new sensors to the left, right, and rear in addition to the central circular line sensor. This allows the robot to immediately detect the white line when it crosses over it.

・Increasing the number of the sensor ports
For the circular line sensor, reading values from each sensor allows us to estimate the current position of the reacting white line.
This enables the robot to return to the court even when it crosses halfway over the white line.

# 【Robots’ Overview / Descriptions Of The Installed Parts 】

# SPONSERS

0

500

1000

1500

2000

15 | 20 | 25 | 30 | 35 | 40

## Kick Power vs. Voltage (Fig.3)

capacitance = 4700μF

(mm)

(V)

Ball Angle

90°

90°

90°

Move
Direction

Fig.B-1 ball-tracking system when ball is near

X°

Fig.B-2 ball-tracking system when ball is far

0

500

1000

1500

2000

2500

220 | 330 | 470 | 560 | 1000 | 2200 | 3300 | 4700

## Kick Power vs. Capacitance (Fig.2)

voltage = 22V

(mm)

(μF)

Autodesk
Fusion

KiCad GitHub

Discord

Google
Spreadsheet

## 2 Debugging components

We have placed menu operation buttons and a small LCD monitor at the rear of the robot.
These are positioned for easy access during a match, allowing us to check sensor values and change the robot’s
Mode without connecting to a computer.

## 8 Solenoid

We have selected Takaha's CB1037 solenoid for the kicker. Among solenoids of similar size in the series, it has a longer stroke and delivers greater kicking force relative to its size, making it ideal for a compact and high-power kicker unit.

## A. Main Board (Robot.1)

This board is equipped with the “Teensy 4.0” main microcontroller, the “BNO055” IMU sensor, the “Twelite UART” communication module for inter-robot communication, the tournament’s official communication module, and various control switches.
All of the data from microcontrollers and sensors on other boards is aggregated here, and this data is used to control the robot.

・Teensy 4.0: It has many serial ports and very high performance, making it suitable for high-precision control using many sensors and sub-microcontrollers.
・BNO055: It allows easy control and has less angular drift compared to other IMU sensors.
・Twelite: It enables easy communication by simply connecting it to the microcontroller via UART.

## 4 IR Sensor

We have chosen the TSSP58038 for the ball detection. By placing 16 of them in a circular pattern on the central board, we can calculate the angle of the ball more accurately.

## B. Drive Board (Robot.1)

This board incorporates a motor driver circuit and a kicker drive circuit.
We have chosen VNH5019 for the motor driver IC, and XL6009 for the voltage booster included to de kicker circuit.
The motor driver IC can handle a power supply voltage of up to 41V, which is more than three times the voltage supplied from the battery, and it supports an extremely high current of 30A, ensuring high durability.
The kicker circuit uses two types of MOSFETs, P-channel and N-channel. One is used for controlling the solenoid, and the other is used to disconnect the circuit during the kick motion.
By isolating the kicker circuit from other circuits during kicking, we can physically block the electrical noise caused by the voltage drop during the kicking motion and the back electromotive force generated when the solenoid's shaft returns. This ensures that no noise affects both the driving power supply and the control power supply.

## 6 Power circuit Board

The power circuit board includes battery protection circuits, and circuits for generating both the drive power supply and control power supply.
The battery protection circuits feature reverse connection protection, overcurrent protection, and over-discharge prevention.
To generate the control power supply, a DC-DC converter is used, which minimizes the electrical noise from the drive power supply, ensuring stable operation of the microcontrollers.

## 3 Ball Capture Detecting Sensor

We have placed an LED on one side of the ball supplement area, and an S4282-51 photodetector IC on the other side, which detects the ball supplement.
This IC responds only to light of a frequency synchronized with the IC itself, allowing it to be used even in daylight or under an indoor lighting without causing false detections, making it ideal for precise control.

## 5 Line Sensor

We have positioned a circular board in the center and a board with a circular cut-out shape on the outer edge.
Sensors placed on the outer edge enable immediate response to the line, and the sensors in the center ensures continuous line detection, even when the robot moves over the line.
The description about the line sensor is summarized in “Robot’s Feature” section.

## 7 Motor

Robot.1 : We use Maxon's RE16 series motors, which offer high efficiency and responsiveness, reducing the robot's power consumption and enabling finer movements.

Robot.2 : We have adopted the DIGILENT IG22 1/19 motor. Despite being lightweight, it offers high responsiveness and speed. Additionally, its affordability makes it an ideal choice for RoboCup soccer robots, which is why we adopted it.

## 9 Frame : A2017

The frame was designed using Autodesk Fusion and machined using a CNC. A2017 Duralumin, known for its excellent durability, allows for a lightweight yet extremely sturdy frame.

Robot.2's concept is to be a "strong robot with stable operation" for soccer competitions, which is a challenging feat to achieve. However, we have implemented various innovations to achieve this goal.
All components installed in Robot.2 have undergone a year-long development and testing process to ensure stability. Additionally, it is designed to place various additional components for adapting to changes in rules.
By completing the robot production process early and allowing sufficient time for adjustments, we can achieve stable operation and develop a "strong robot".

Fig.A a shape of line sensor

Fig.1. The circuit of the kicker mechanism

FET1 and FET2 are controlled by signals from the microcontroller. When FET1 is set to HIGH, the connected capacitors (C6, C7) will be charged up. When FET2 is set to HIGH, the solenoid
operates using the power stored in the charged capacitors. Setting FET1 to LOW isolates the kicker circuit from all other circuits using P channel MOSFET, effectively blocking electrical noise.

Robot.1's concept is to be a "robot with a low center of gravity and high maintenance performance". In a robot that moves freely around the court at high speed, having a low center of gravity is crucial. A low center of gravity allows the robot to execute turns and speed changes with minimal force, reducing power consumption and enabling more precise movements. However, achieving a low center of gravity often means designing the robot to be compact and densely packed with components internally, potentially compromising maintenance accessibility. To address this challenge, Robot.1 has been designed with a reduced number of components. Most parts and boards can be quickly removed and replaced, ensuring ease of maintenance despite its low-profile design.

Visual
Studio Code

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
# Robo.1

## Robo.1

## Robo.2

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
# Robo.2

3

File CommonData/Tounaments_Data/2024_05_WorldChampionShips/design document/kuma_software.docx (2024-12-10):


OpenMVによるカラートラッキング fig**(openmvideの画面)はOpenMVによる色とりの例である。全方認識可能なミラーを使用することにより、コート内を360度見ることが可能である。使用例としては、ゴールの色やコートの色の閾値をアークタンジェントとし、角度を計算し、同時にカメラ中心との距離を算出している。算出された角度と距離はシリアル通信でteensy（メインマイコン）に送られる。角度を用いて、ゴールの中心方向とロボットのずれを計算し、PID制御を行うことでゴール方向を向くことができる。ジャイロセンサーのみを用いたときよりもゴール率は高くなる。しかし、光の入り方によってゴールの見え方が変化する問題が起きた。その対策としてカメラから得られる画像のガンマ値、コントラスト、明度を変更した。これによってその場に応じてゴールの見え方を変えることができた。


アタッカー機について 以前はロボットが攻撃をするとき、ゴールが見えているときはゴール方向を向き、ゴールが見えていないときはジャイロセンサーを用いて前方向を向くようにしていた。 しかし、全国大会で問題が発覚した。それは、ゴールが見えるようになる境界でゴールが見えたり見えなかったりすることでジャイロセンサーでの方向制御とゴール方向での方向制御が頻繁に切り替わり、スムーズな動きができなかったことである。そのため、ボールを持った時、またはゴールに近くなったときにゴール方向を向く方法に変更した（fig上図）。これによってゴール方向とジャイロ方向の向きが頻繁に切り替わることを防ぐことができ、ゴール率をあげることが出来た。

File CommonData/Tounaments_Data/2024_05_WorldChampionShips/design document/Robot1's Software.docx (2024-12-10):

Robot1’s Software


- ディフェンスプログラムの処理

Fig.1 Defender System

Robot.1は主にディフェンダーの役割を果たします。

ディフェンスのシステムは、円形ラインセンサーとボールセンサーの2つを用いて実装しています。

ロボットはゴール前の白線の上にとどまり、ボールの反応角度によって移動・停止します。

Fig.1はディフェンスシステムを図示したもので、大きな丸(半透明)はロボット、その中にある小さな丸(赤や白)はラインセンサーを示しています。Fig.1 ① において、反応したラインセンサーを結ぶ線分の垂線の角度を基準として、ボールが垂線角度±15°であるときは停止します。

また、Fig.1 ② において、反応したセンサーを結ぶ線分の垂線角度±15°を超えたときは、ボールがある方向のラインセンサーの角度方向に移動します。

以前は、白線上で左右のうちボールのある方向にしか動かなかったため、ゴール前白線に戻る処理が実行されることで白線上の移動がスムーズに行われません。しかし、移動方向をラインセンサーの反応角度に変更することで、「ゴール前白線にとどまる」「ボール方向に移動する」の2つを同時に実現することができ、よりスムーズに相手からのボールのシュートを防ぐことができました。


- ラインセンサーのアルゴリズム

Fig.2 An algorithm of Circle Shape Line Sensor

Robot.2もそうですが、私たちのロボットには円形ラインセンサーが搭載されています。

円形ラインセンサーを用いることで、ロボットが白線をどのように踏んでいるのかが正確に検知できるため、アウトオブバウンズ対策の正確性向上に大きく役立ちます。

Fig.2は円形ラインセンサーのアルゴリズムについて図示したものです。図にある3つの白線において、右側がコート内、左側がアウトゾーンです。

①・②は、反応しているセンサーをもとに、反応したセンサーとは逆の方向に移動しています。

③では、反応しているセンサーを元にした移動方向はアウトゾーンに進む方向ですが、前回の反応角度と比較して、角度が大きく変化していたら「半分以上超えた」という風に検知することで、反応角度と逆に進みアウトオブバウンズを防いでいます。このように、円形ラインセンサーはロボットが半分以上ラインを越えても正しく移動方向を算出することができます。

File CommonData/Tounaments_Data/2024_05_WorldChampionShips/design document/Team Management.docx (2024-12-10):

Team Management

私たちのチームは、主にハードウェアチームとソフトウェアチームに分かれています。そのため、

実際のチーム活動において、どちらのチームが現在どのようなことをしているのかがわかりづらい状況が多くありました。また、大会までの期間が短く、確保できる作業時間が限られていました。

そこで、私たちはチーム活動について、大きく2つの点で改善をしました。

グラフィカル ユーザー インターフェイス, テキスト, アプリケーション

Fig.A Task Management Tool (Google Spreadsheet) Fig.B Communication Tool (Discord)

<タスクの可視化・コミュニケーションの円滑化>

タスクの可視化という面で、私たちはGoogle Spreadsheetというツールを使用しました。

Google Spreadsheetでは、主に各チームメンバーのタスクをリスト化・管理しています。(Fig.A) これはオンライン上で使用することができるため、どんな時でも各メンバーのタスクを確認できます。また、チームメンバーは誰でもタスクリストを追加・削除・編集することができるため、何か問題が生じた際も、タスクをほかのチームメンバーに渡したり、他のメンバーのタスクを受け持ったりすることが瞬時にでき、それをチームメンバー全員が確認することができます。

このツールによって、タスクを明確に可視化することができ、チーム活動をスムーズに行うことができました。

また、コミュニケーションの円滑化という面では、Discordというツールを用いました。

Discordでは、主にチーム活動における議論を行っています。(Fig.B) Discussion機能を使用することで、

トピックごとにチャンネルを作成することができ、1つのトピックについて円滑な議論をすることができます。

ssSS


<ワークフローの改善>


Fig.3 Single Workflow System (From Our Presentation Poster)

F ig.4 Multiple Workflow System (From Our Presentation Poster)

私たちは、世界大会までの準備期間が短く、作業を効率化する必要がありました。そこで、私たちは

「ワークフローの改善」を行いました。

今までは、Fig.1のように、タスクを1つずつこなしていくようなワークフローの体系をとっていました。

これは、全員が各タスクの確認を行うことで、より確実な成果を生むことができるというメリットが

ありますが、1つずつしかタスクを処理することができないため、時間がかかるというデメリットがあります。また、ソフトウェア開発において表面化した問題をハードウェアにフィードバックすることができないため、ロボットの改善がしにくいという問題があります。

そこで、Fig.2のように、各チームメンバーが並行して複数の作業を行う、マルチタスクフローという形をとりました。Fig.2で示しているのは多くのタスクの中から抜粋した一部のタスクですが、図のように

作業を並行して行うことで、ソフトウェアからハードウェアへのフィードバックが可能になり、設計段階でのシステム変更が可能になったほか、ロボットが完成する前に各部品の動作確認ができるため、

完成後のロボットのプログラム調整をスムーズに行うことができました。

以上のようなチーム活動の改善を行うことで、短い期間の中で、ロボットの開発をスムーズに行い、チーム活動を円滑に進めることができました。

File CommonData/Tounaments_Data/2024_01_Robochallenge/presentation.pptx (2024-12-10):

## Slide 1


チームメンバー

松田 魁琉 / 目野 優輝
石原 廉太郎 / 熊抱 崚太

所属ブロック

九州ブロック 北九州ノード

GitHub Logos and Usage · GitHub
白い背景に分離された丸い twitter ロゴ | プレミアムベクター

@munako_artemis


Artemis Homepage


ロボットの概要


2024シーズンから円形状のラインセンサを搭載しました。
今までは十字のラインセンサを用いていましたが、十字だと
一定の角度で反応しない場合が存在していましたが、
円形ラインセンサを搭載することでどの角度からでも一定の距離で必ず反応させることができるようになりました。

円形ラインを用いたライン制御

また、円形ラインを用いることで、ゴール前の白線を
ロボットが半分以上超えてしまった際にもコート内に
正確に戻ることができるようになりました。
これは、ラインセンサが反応した白線の角度を2ループ分記憶し、前回の角度を今回の角度のずれを比較することで実現
しています。

ロボットは左進行

コート内

左に反応が寄っているので右に動く

ロボットは左進行

コート内

右に反応が寄っているので左に動くが…？

前回との比較で「行き過ぎた」と判断して反応の寄り方と逆
方向に移動してアウトを防ぐ

十字ラインだと反応しない
角度が存在するが…

円形ラインにすることで
どの角度でも反応するように

ゴールへのアプローチ

私たちのロボットには全方位カメラを搭載しています。
コートを全方位見渡すことで、相手ゴールの認識を
行うことができ、ゴールの角度データを利用することで
ロボットがゴールの方向を向くことができ、常に前を向く
状態よりも圧倒的得点率を叩き出します。

デザインと機能性を兼ね備えたUI

私たちのロボットには、ロボットの
データを可視化・操作するためのUI
機構を搭載しています。具体的には、
ロボット後方部にLCDとしてSSD1306、
操作用のボタン・スイッチを計4つ
搭載しています。
LCDは、センサーのデータやロボットの現状、操作盤としての役割を果たしています。
スイッチを用いることで、ロボットのスタート・ストップ、画面の切り替え等を行えるようにしています。

- 搭載している部品
・バッテリー　　　　:　KyPom 3Cell 1300mA
・モータードライバ　:　DSR-1202
・モーター　　　　　:　IG22 19:1 x 4
→ 応答性の高さから採用しました。
・メインマイコン　　:　Teensy 4.0 x 1
→ シリアル用ピンの多さから採用しました。
・サブマイコン　　　:　Seeeduino Xiao x 3
→ ジャイロセンサ・ラインセンサ・ボールセンサの処理に使用。
・ボールセンサ　　　:　TSSP58038 x 8
→ ボールから発せられる赤外線を読み取り、サブマイコンで
計算を行ってボールの角度を距離を算出しています。
・ラインセンサ　　　:　S4282-51 x 16
→ 光変調フォトICと呼ばれるものを使用し、白線の判別をしています。
ベクトルの考えを用いて白線の角度を算出しています。
・ジャイロセンサ　　:　L3GD20H x 1
→ 主にロボットの姿勢を制御するために用いています。
・カメラ　　　　　　:　OpenMV H7 x 1
→ カメラ導入コストの低さから採用しました。
今回の機体では全方位ミラーを用いて360度の方向を監視しています。

ゴールを向くことでボールを入れることができる

これらがなければ、ロボットと
パソコンをケーブルで接続し、
わざわざデータを出力するという
工程を踏まなければなりません。
Uiはデザインとともに機能性を
兼ね備えた合理的な機構と言えます。


このままではゴールに
入れることはできないが…

ゴール

ゴール

ロボット製作は環境から

私たちのチームではロボット製作をより円滑に行うために様々なツールを用いています。これらのツールを用いることにより、
今まで時間がかかっていた作業等を大幅に削減することが
できるようになりました。

＜私たちが使用しているツール＞
・機体設計 : Fusion360
・基板設計 : KiCad 6.0
・ファイル・バージョン管理 : Github
・プログラム開発 : VSCode + PlatformIO(拡張機能)
・コミュニケーションツール : Discord, Asana

弊チームにはスポンサーが付いています。
スポンサーの方々のお陰で私たちのロボットが成り立っています、本当にありがとうございます。
・JLCPCB 様
基板発注時の金銭面の
サポートをして下さっています。

スポンサー

KiCad 5.1.10 Release - TALPKEYBOARD BLOG
GitHub を無料でダウンロード。2023 年最新版
Visual Studio Code - Wikipedia

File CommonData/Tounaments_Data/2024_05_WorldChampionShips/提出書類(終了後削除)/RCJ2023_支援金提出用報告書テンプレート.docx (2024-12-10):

リーグ | Soccer LightWeight | チーム名 | Munako Artemis
メンバー | 石原 廉太郎 / 松田 魁琉 / 目野 優輝 / 熊抱 崚太
所属ブロック | 九州ブロック | 所属 | 北九州ノード

大会参加の目的（目標）

・世界1位を獲る

・世界中のロボカップ参加者と交流し、様々な経験をする

大会の様子（会場の様子，試合の様子，チーム間交流の様子など）

・ロボカップシニアリーグ(SSL、中型リーグなど)がすぐそばに設置されており、会場的には端の方にL字で設置されていた。(パドックはLW/OPENで別)

・パドックは人数関係なく1つの机で、コンセントは共用。スペースは比較的狭めでゴチャゴチャしていた印象がある。

・全体的に緩めで、とにかく「大会に参加して楽しむ」を意識されていたような気がする。

・基本的にスコア管理の人がスコアをつける(iPad等での管理は無し)以外は基本的に全国大会と同じ。

・SuperTeamがとても盛り上がっていた。海外チーム間との交流もこの時に盛んに行った。

国内大会と違っていたと感じた点（良い点，悪い点）

<良い点>

・コミュニケーションモジュール

→ワンタッチでロボットのStop/Startができるという取り組みはとてもいいと思った。

・チーム間の交流のしやすさ

→パドックが基本隣接して隣同士で置いてあるため、チームの間での交流が必然的に

発生していた。

<悪い点>

・審判のルール熟知度

→ルールをよくわかっていないのか、コート端のライン(≠ゴール前白線)のところで

プッシングをとっていたり、過去のルールが適用されたままだったりの試合が

いくつか見受けられた。

また、ルールとは直接関係ないが、スコア管理が杜撰であった試合もあった。

・外野からの野次

→時々相手チームのメンター？からの野次が飛んでいた。

大会参加の成果（学んだこと，目標の達成度）

・アウトオブバウンズ対策の重要性

→基本的に「ロボットがずっとコート内にいるチームが強い」ため、白線から出ない

という当たり前のことを正確に行えるチームがとても強かった。

(特にEdge。ただ他のチームもラインから出ることは少なかった。)

・プッシング

→現状白線上にとどまりボールを受け止める(もしくはロボットとの押し合い)

ロボットがとても強い(=主にプッシングルールの存在)

ある程度の精度のキーパーであると、余程のことがない限りゴールには基本的に

入れることができなかった。(中国 UGAMM-SOCCER のキーパーは特に)

遠距離から斜めにキッカーで蹴り飛ばすなどの工夫が必要。

・目標について

→惜しくも世界大会優勝という目標をかなえることはできなかった。

しかし、1か月という短い準備期間の中で、総合3位・Top Poster & Presentation

という賞を持ち帰ることができたのはとても大きい。

また、海外のチーム(国内然り)からたくさん学べることがありとても面白かった。

大会参加を受けて日本のロボカッパーへのメッセージ

・日々の努力が大切

ロボットは一朝一夕でできるものではない。それはハードウェア然りソフトウェア然り。だからこそ、常日頃からロボットと向き合って努力することが大切。

世界大会で使った知識や経験は、基本的に日々の活動で身に着けた知識の応用がほとんど。実際に世界大会で強かったロボットは毎日調整していたのだなと感じるようなロボットだった。

・やっぱり世界大会は楽しかった

全国大会ももちろん楽しいが、世界大会はそれ以上に楽しかった。Super Teamやいろんな国の人との交流をし、ハプニングが起き、とにかくいろんなことが起きてとても楽しかった。全国大会を勝ち抜くことはそう容易ではない(私たちもギリギリ行くことができた)が、その先に待っているのはとても面白い光景だから、ぜひ世界大会に向けて活動を頑張ってほしいと思う。

・予備の準備

部品やマイコンの予備の準備はとても大切。だが、それ以上に、問題が発生したときにどう対処するかという準備がとても重要だった。

(準決勝前にモータードライバのマイコンが焼けた。原因特定に時間がかかり、準決勝中にロボットを修理することができなかった。)

成績（公式に残るものだけでなく予選の結果，交流戦などできるだけ詳しく）

・Round 1 vs. Oi_DENGIKEN（日本）●　５－６

・Round 2 vs. Andys Geese（カナダ）○　３１－０

・Round 3 vs. Bodensee-Luchse（ドイツ）○　２７－７

・Round 4 vs. RBL Stieren（メキシコ）○　１６－８

・Round 5 vs. UGAMM-SOCCER（マカオ）●　４－１２

・Round 6 vs. Righteousness（マカオ）△　８－８

・Round 7 vs. ETC autoPrikratki CRO Team（クロアチア）○　１３－４

・Round 8 vs. Edge（日本）○　１３－５

・Semi-Final　 vs. UGAMM-SOCCER（マカオ）●　１－１４

・3rd place play-off 　vs. Zenith（オーストラリア）○　２５－１　３位

会場，試合，対戦相手など記録となる写真（数枚）


その他

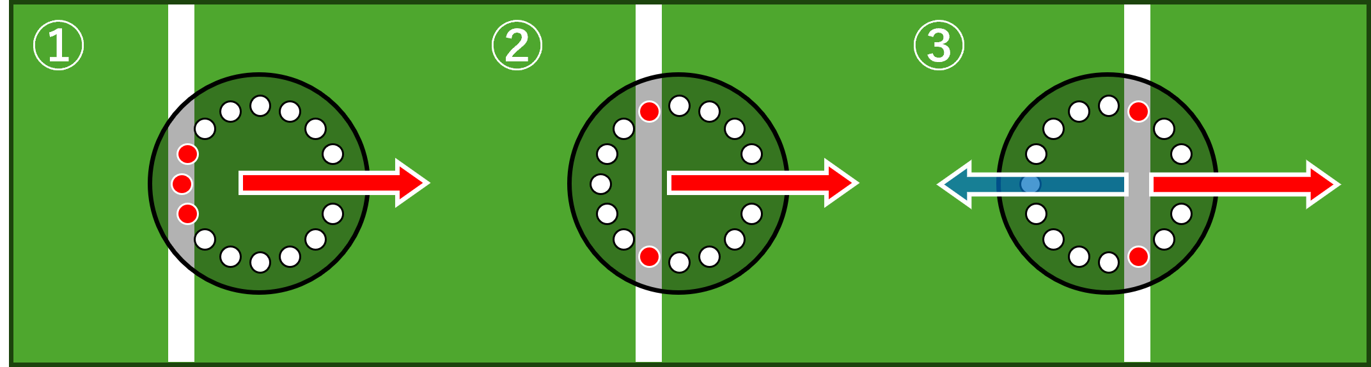
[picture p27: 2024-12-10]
CommonData/Tounaments_Data/2024_05_WorldChampionShips/design document/Engel Line Sensor.png

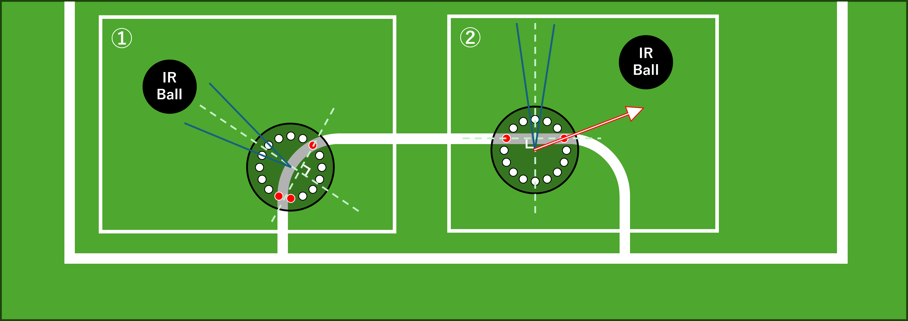
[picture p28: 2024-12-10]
CommonData/Tounaments_Data/2024_05_WorldChampionShips/design document/Defender.png

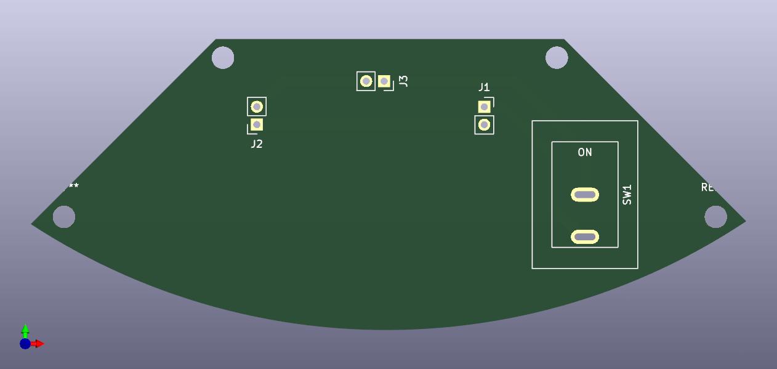
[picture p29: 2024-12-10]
Project_Testing_AkizukiMotor/Hardware/3d_data/supply_board_texture/supply_board.jpg

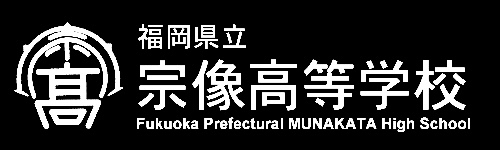
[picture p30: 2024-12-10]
Project_KOKUROU_dev.1/Others/ステッカー/up_ZL7NWUP5header_01.jpg

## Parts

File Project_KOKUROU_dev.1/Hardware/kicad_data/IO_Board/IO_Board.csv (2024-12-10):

Comment | Designator | Footprint | LCSC
WS2812B | D1,D2,D3 | LED_SMD:LED_WS2812B_PLCC4_5.0x5.0mm_P3.2mm | C2761795
Conn_01x08_Socket | J1 | Connector_PinHeader_2.54mm:PinHeader_1x08_P2.54mm_Vertical
SW_Push | SW1,SW2,SW3 | Button_Switch_THT:SW_PUSH-12mm_Wuerth-430476085716
SW_DIP_x01 | SW4 | Connector_JST:JST_XH_B2B-XH-A_1x02_P2.50mm_Vertical

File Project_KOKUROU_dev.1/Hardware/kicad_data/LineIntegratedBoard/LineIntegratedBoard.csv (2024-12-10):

Comment | Designator | Footprint | LCSC
Conn_01x08_Socket | J1,J2,J3 | Connector_PinHeader_1.27mm:PinHeader_1x08_P1.27mm_Vertical
Conn_01x05_Socket | J4 | Connector_PinHeader_1.27mm:PinHeader_1x05_P1.27mm_Vertical
CD74HC4067SM | U1 | Package_SO:SSOP-24_5.3x8.2mm_P0.65mm | C98457
SeeeduinoXIAO | U2 | Seeeduino_Xiao:Seeeduino XIAO-MOUDLE14P-2.54-21X17.8MM

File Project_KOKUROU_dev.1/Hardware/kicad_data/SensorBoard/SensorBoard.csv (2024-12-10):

Comment | Designator | Footprint | LCSC
SSD1306 | Brd1 | SSD1306:128x64OLED
C_Small | C1,C2,C3,C4,C5,C6,C7,C8,C9,C10,C11,C12,C13,C14,C15,C16 | Capacitor_SMD:C_0402_1005Metric
C | C17,C19 | Capacitor_SMD:CP_Elec_5x5.4
C | C18 | Capacitor_SMD:C_0402_1005Metric
WS2812B | D1,D2,D3,D4,D5,D6,D7,D8,D9,D10,D11,D12,D13,D14,D15,D16,D17,D18,D19,D20,D21,D22,D23,D24,D25,D26,D27,D28,D29,D30,D31,D32 | WS2812B:LED_WS2812B-Mini_3.5x3.5mm
Conn_01x10_Socket | J1 | Connector_IDC:IDC-Header_2x05_P2.54mm_Vertical
R_Small | R1,R2,R3,R4,R5,R6,R7,R8,R9,R10,R11,R12,R13,R14,R15,R16 | Capacitor_SMD:C_0402_1005Metric
SW_Push | SW1,SW2 | Button_Switch_THT:SW_PUSH_6mm_H5mm
CD74HC4067SM | U1 | Package_SO:SSOP-24_5.3x8.2mm_P0.65mm
SeeeduinoXIAO | U18 | Seeeduino_Xiao:seeeduinoXIAO
open_mv | U19 | OpenMV:OpenMV
TSSP58038 | U2,U3,U4,U5,U6,U7,U8,U9,U10,U11,U12,U13,U14,U15,U16,U17 | TSSP58038:TSSP58038
L7805 | U20 | Seeeduino_Xiao:3端子レギュレータ

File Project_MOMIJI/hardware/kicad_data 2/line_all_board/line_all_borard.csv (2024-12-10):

Comment | Designator | Footprint | LCSC
C_Small | C1,C2,C3,C4,C5,C6,C7,C8,C9,C10,C11,C12,C13,C14,C15,C16,C17,C18,C19,C20,C21,C22 | Capacitor_THT:C_Disc_D3.4mm_W2.1mm_P2.50mm
C_Small | C23 | Capacitor_THT:CP_Radial_D5.0mm_P2.50mm
LED | D1,D2,D3,D4,D5,D6,D7,D8,D9,D10,D11,D12,D13,D14,D15,D16,D17,D18,D19,D20,D21,D22 | LED_THT:LED_D3.0mm
Conn_01x05_Female | J1 | Connector_JST:JST_XH_B5B-XH-A_1x05_P2.50mm_Vertical
Line_sennsor | U1,U2,U3,U4,U5,U6,U7,U8,U9,U10,U11,U12,U13,U14,U15,U16,U17,U18,U19,U20,U21,U22 | Line_Sensor:Line_Sensor_SMD
SeeeduinoXIAO | U23 | Seeeduino_Xiao:seeeduinoXIAO
CD74HC4067SM | U24 | Package_SO:SSOP-24_5.3x8.2mm_P0.65mm | C98457

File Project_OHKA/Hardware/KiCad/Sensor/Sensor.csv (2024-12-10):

Comment | Designator | Footprint | LCSC
SSD1306 | Brd1 | Connector_PinHeader_2.54mm:PinHeader_1x04_P2.54mm_Vertical
C_Small | C1,C2,C3,C4,C5,C6,C7,C8,C9,C10,C11,C12,C13,C14,C15,C16 | Capacitor_SMD:C_0402_1005Metric
C | C17,C18,C19 | Capacitor_THT:C_Disc_D3.0mm_W1.6mm_P2.50mm
Conn_01x10_Socket | J1 | Connector_IDC:IDC-Header_2x05_P2.54mm_Vertical
R | R1,R2,R3,R4,R5,R6,R7,R8,R9,R10,R11,R12,R13,R14,R15,R16 | Resistor_SMD:R_0402_1005Metric | C25741
R_Small | R17,R18
R | R19,R20,R21 | Resistor_THT:R_Axial_DIN0204_L3.6mm_D1.6mm_P5.08mm_Horizontal
SW_Push | SW1,SW2,SW3,SW4 | Button_Switch_THT:SW_PUSH_6mm_H4.3mm
TSSP58038 | U1,U2,U3,U4,U5,U6,U7,U8,U9,U10,U11,U12,U13,U14,U15,U16 | OptoDevice:Vishay_MINICAST-3Pin
CD74HC4067SM | U17 | Package_SO:SSOP-24_5.3x8.2mm_P0.65mm
Seeeduino_Xiao | U18 | Seeeduino_Xiao:seeeduinoXIAO
open_mv | U19 | Connector_JST:JST_XH_B3B-XH-A_1x03_P2.50mm_Vertical

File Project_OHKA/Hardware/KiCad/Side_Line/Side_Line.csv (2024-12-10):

Comment | Designator | Footprint | LCSC
LED | D1,D2,D3,D4,D5,D6 | LED_THT:LED_D3.0mm_Clear
Conn_01x04_Socket | J1 | Connector_PinHeader_2.54mm:PinHeader_1x04_P2.54mm_Vertical
Q_Photo_NPN | Q1,Q2,Q3,Q4,Q5,Q6,Q7 | LED_THT:LED_D3.0mm_Clear
R | R1,R2,R3,R4,R5,R6 | Resistor_SMD:R_0603_1608Metric
R_Small | R7
R_Potentiometer_Trim_US | RV1 | Potentiometer_SMD:Potentiometer_Bourns_TC33X_Vertical

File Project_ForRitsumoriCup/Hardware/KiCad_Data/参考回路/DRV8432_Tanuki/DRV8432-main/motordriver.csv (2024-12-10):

Comment | Designator | Footprint | LCSC
0.1uf | C1 | Connector_JST:JST_VH_B2P-VH_1x02_P3.96mm_Vertical | C14663
0.1uf | C2, C3, C4, C5 | Capacitor_SMD:C_0603_1608Metric | C14663
200u | C6 | Capacitor_SMD:CP_Elec_5x5.9 | C2887271
1uf | C7 | Capacitor_SMD:C_0805_2012Metric | C28323
DRV8432DKD | IC1 | SamacSys_Parts:SOP65P1420X360-36N
Conn_01x06_Female | J1, J2 | Connector_PinHeader_2.54mm:PinHeader_1x06_P2.54mm_Vertical
47k | R1 | Resistor_SMD:R_0603_1608Metric | C25819
1 | R2 | Resistor_SMD:R_0603_1608Metric | C22936
10k | R3 | Resistor_SMD:R_0603_1608Metric | C25804

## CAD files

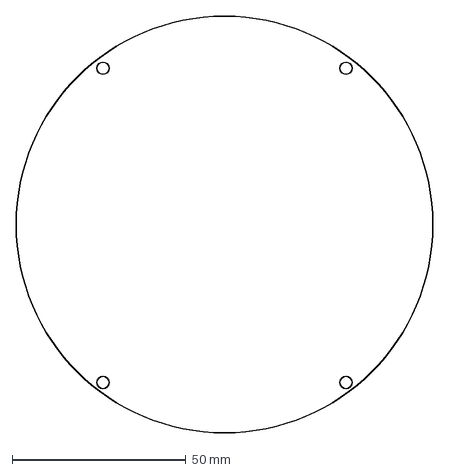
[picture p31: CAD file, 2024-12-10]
Project_DefencerByAsahi/Hardware/kicad_data/main_board/main_board_nocenter.dxf
120.0 x 120.0 mm

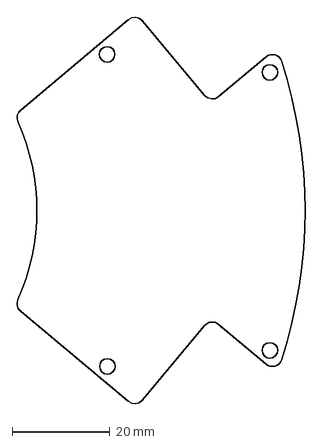
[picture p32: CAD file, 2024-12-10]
Project_DefencerV2_ByAsahi/Hardware/kicad_data/main_board/main_board.dxf
60.8 x 79.7 mm

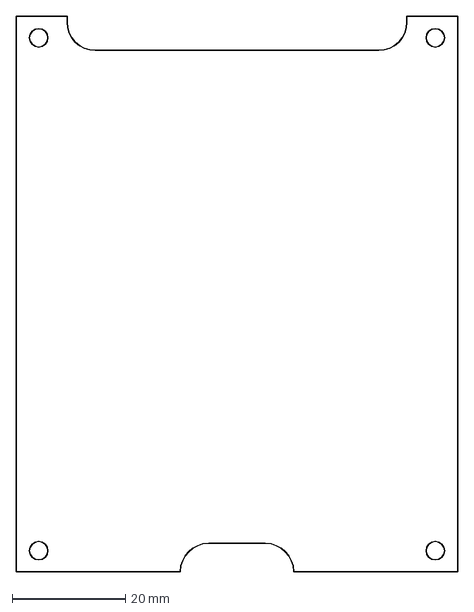
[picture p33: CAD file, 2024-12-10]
Project_ForKitakyusyuOpen/Hardware/kicad_data/order/main_board/main.dxf
78.0 x 98.0 mm

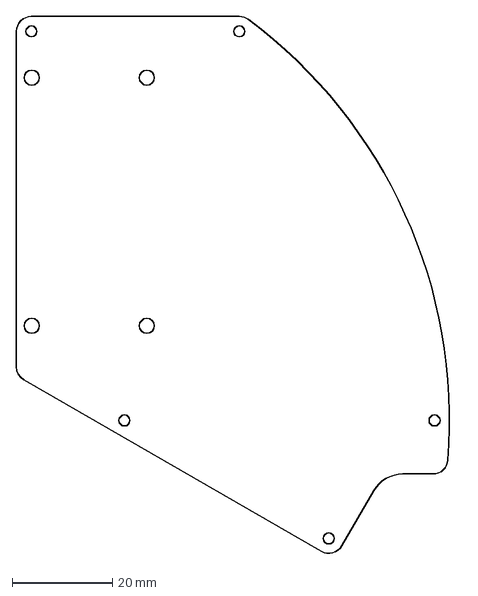
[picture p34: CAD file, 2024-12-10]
Project_KOKUROU_dev.1/Hardware/kicad_data/MainBoard/MainBoard.dxf
89.0 x 107.8 mm

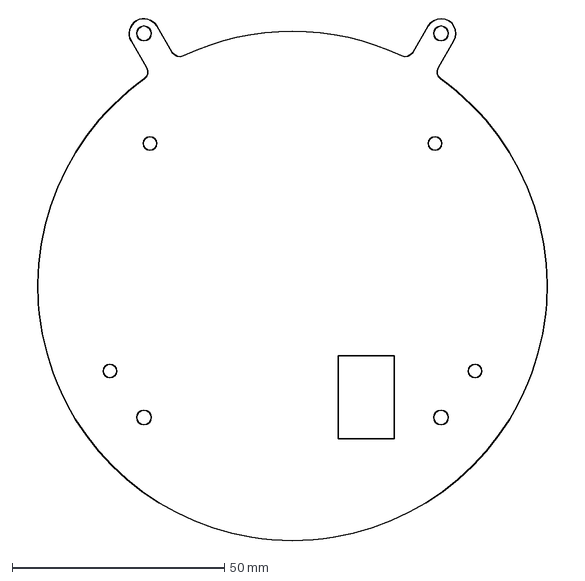
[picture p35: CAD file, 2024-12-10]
Project_MOMIJI/hardware/kicad_data 2/main_board/main_board.dxf
130.2 x 123.5 mm

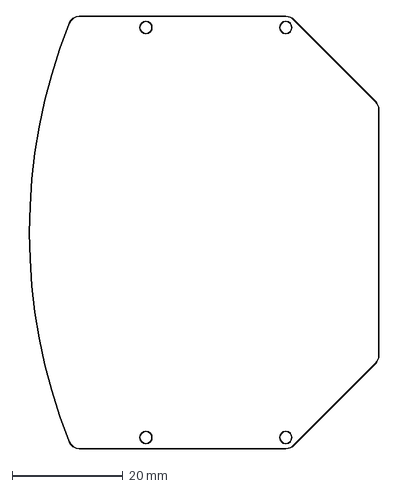
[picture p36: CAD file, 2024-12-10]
Project_OHKA/Hardware/KiCad/Main/Main.dxf
65.4 x 77.9 mm

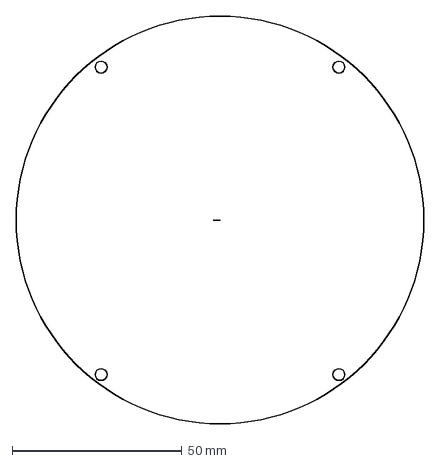
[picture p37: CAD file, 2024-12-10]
Project_DefencerByAsahi/Hardware/kicad_data/main_board/main_board.dxf
120.0 x 120.0 mm

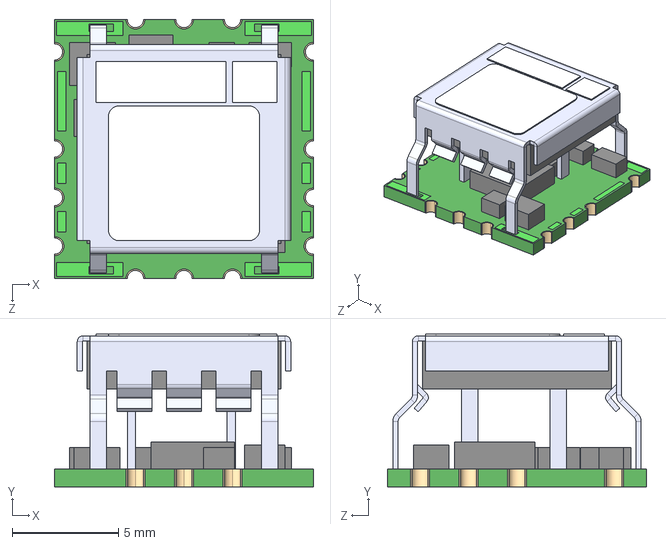
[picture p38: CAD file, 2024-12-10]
CommonData/KiCad_Library/OKL-T_6-W12N-C/OKL-T_6-W12N-C.step
12.2 x 7.19 x 12.2 mm

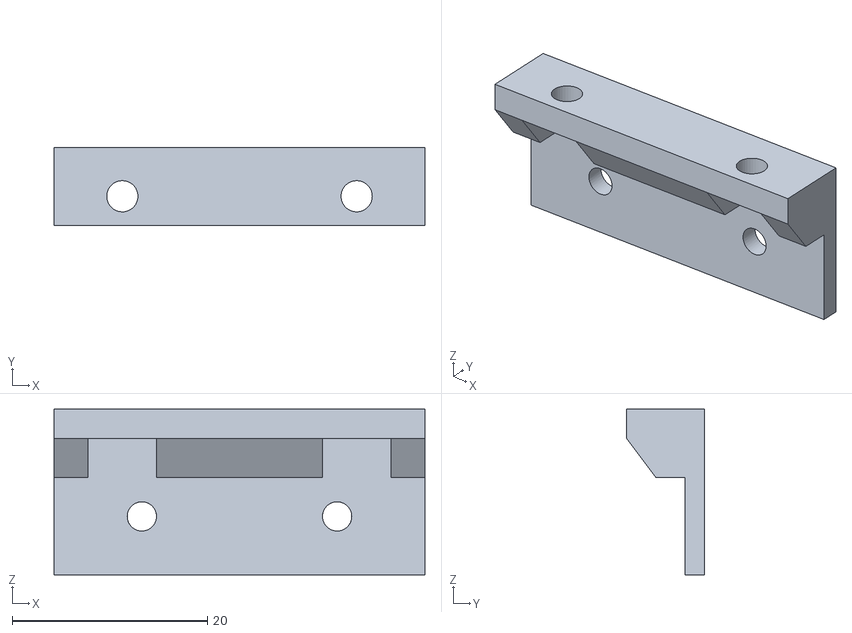
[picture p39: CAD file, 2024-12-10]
Project_DefencerByAsahi/Hardware/3D_data/Kicker_Fixture.stl
38.0 x 8.00 x 17.0

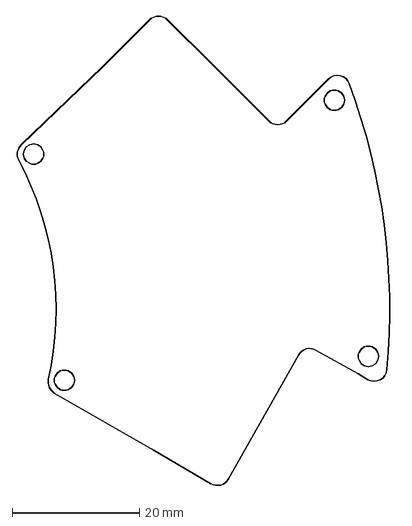
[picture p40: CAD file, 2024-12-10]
Project_DefencerByAsahi/Hardware/kicad_data/kicker_board/kicker_board.dxf
59.8 x 74.0 mm

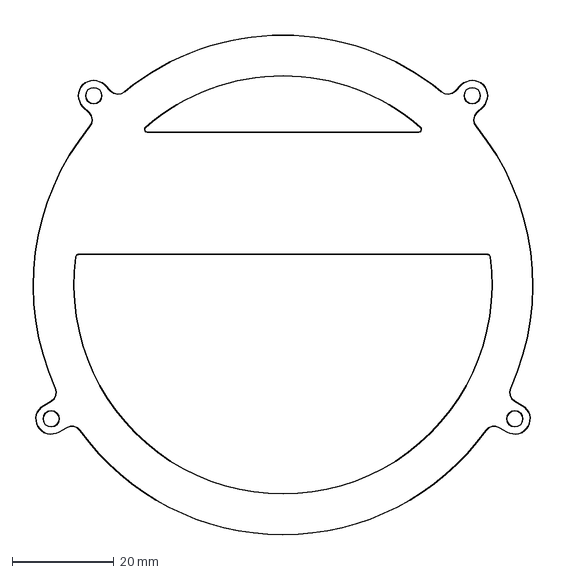
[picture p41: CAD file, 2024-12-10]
Project_DefencerByAsahi/Hardware/kicad_data/line_board/line_board_nocenter.dxf
104.7 x 101.7 mm

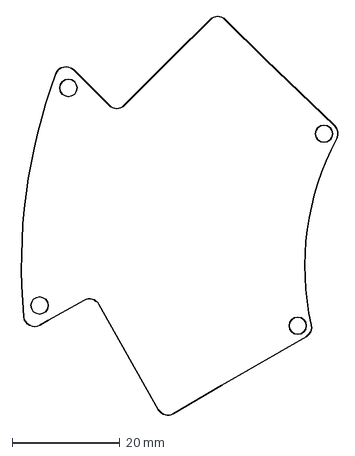
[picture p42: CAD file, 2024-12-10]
Project_DefencerByAsahi/Hardware/kicad_data/psu_board/psu_board.dxf
59.8 x 74.0 mm

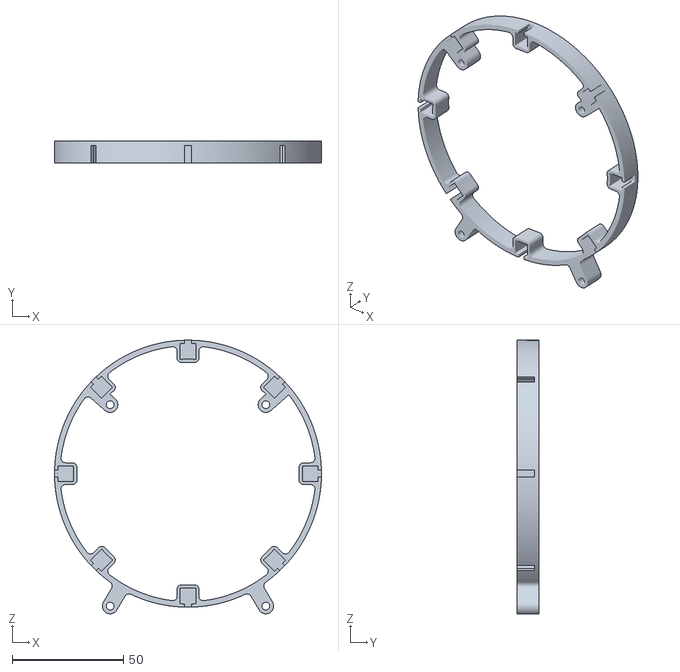
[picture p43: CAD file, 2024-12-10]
Project_DefencerV2_ByAsahi/Hardware/3d_data/ballsensor_hider/BallSensor_HIder v6.stl
120.0 x 10.0 x 123.0

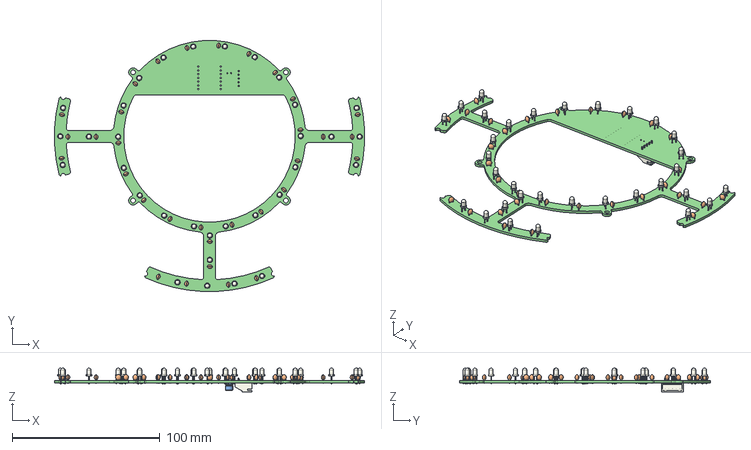
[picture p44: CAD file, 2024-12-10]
Project_DefencerV2_ByAsahi/Hardware/3d_data/Circuit_Boards/engel_line_board_v2.step
209.7 x 169.8 x 16.1 mm
_autosave-engel_line_board_v2 PCB

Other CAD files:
Project_DefencerV2_ByAsahi/Hardware/3d_data/dribbler/SensosBoard_Fixture.stl
Project_DefencerV2_ByAsahi/Hardware/3d_data/hold_sensor/Hold_Sensor_Left.stl
Project_DefencerByAsahi/Hardware/3D_data/Battery_Cover.stl
Project_DefencerByAsahi/Hardware/3D_data/Kicker_Front_Board_Fixture.stl
Project_DefencerByAsahi/Hardware/3D_data/オムニ2024-Complete v4.f3z
Project_DefencerByAsahi/Hardware/kicad_data/line_board/line_board.dxf
Project_DefencerV2_ByAsahi/Hardware/3d_data/Omniwheel/Omni_Fixture v3.stl
Project_DefencerV2_ByAsahi/Hardware/3d_data/Omniwheel/Omniwheel_Fixed.stl
Project_DefencerV2_ByAsahi/Hardware/3d_data/Omniwheel/Omniwheel_byAsahi.stl
Project_DefencerV2_ByAsahi/Hardware/3d_data/Omniwheel/omniwheel_Fixed_v2.stl
Project_DefencerV2_ByAsahi/Hardware/3d_data/ballsensor_hider/BallSensor_Hider.stl
Project_DefencerV2_ByAsahi/Hardware/3d_data/dribbler/Dribbelr_SideFixture_v18.stl
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

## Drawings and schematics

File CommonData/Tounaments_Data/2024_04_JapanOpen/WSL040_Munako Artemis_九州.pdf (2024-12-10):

福岡県立宗像高等学校 | 九州ブロック 北九州ノード

# チームメンバー

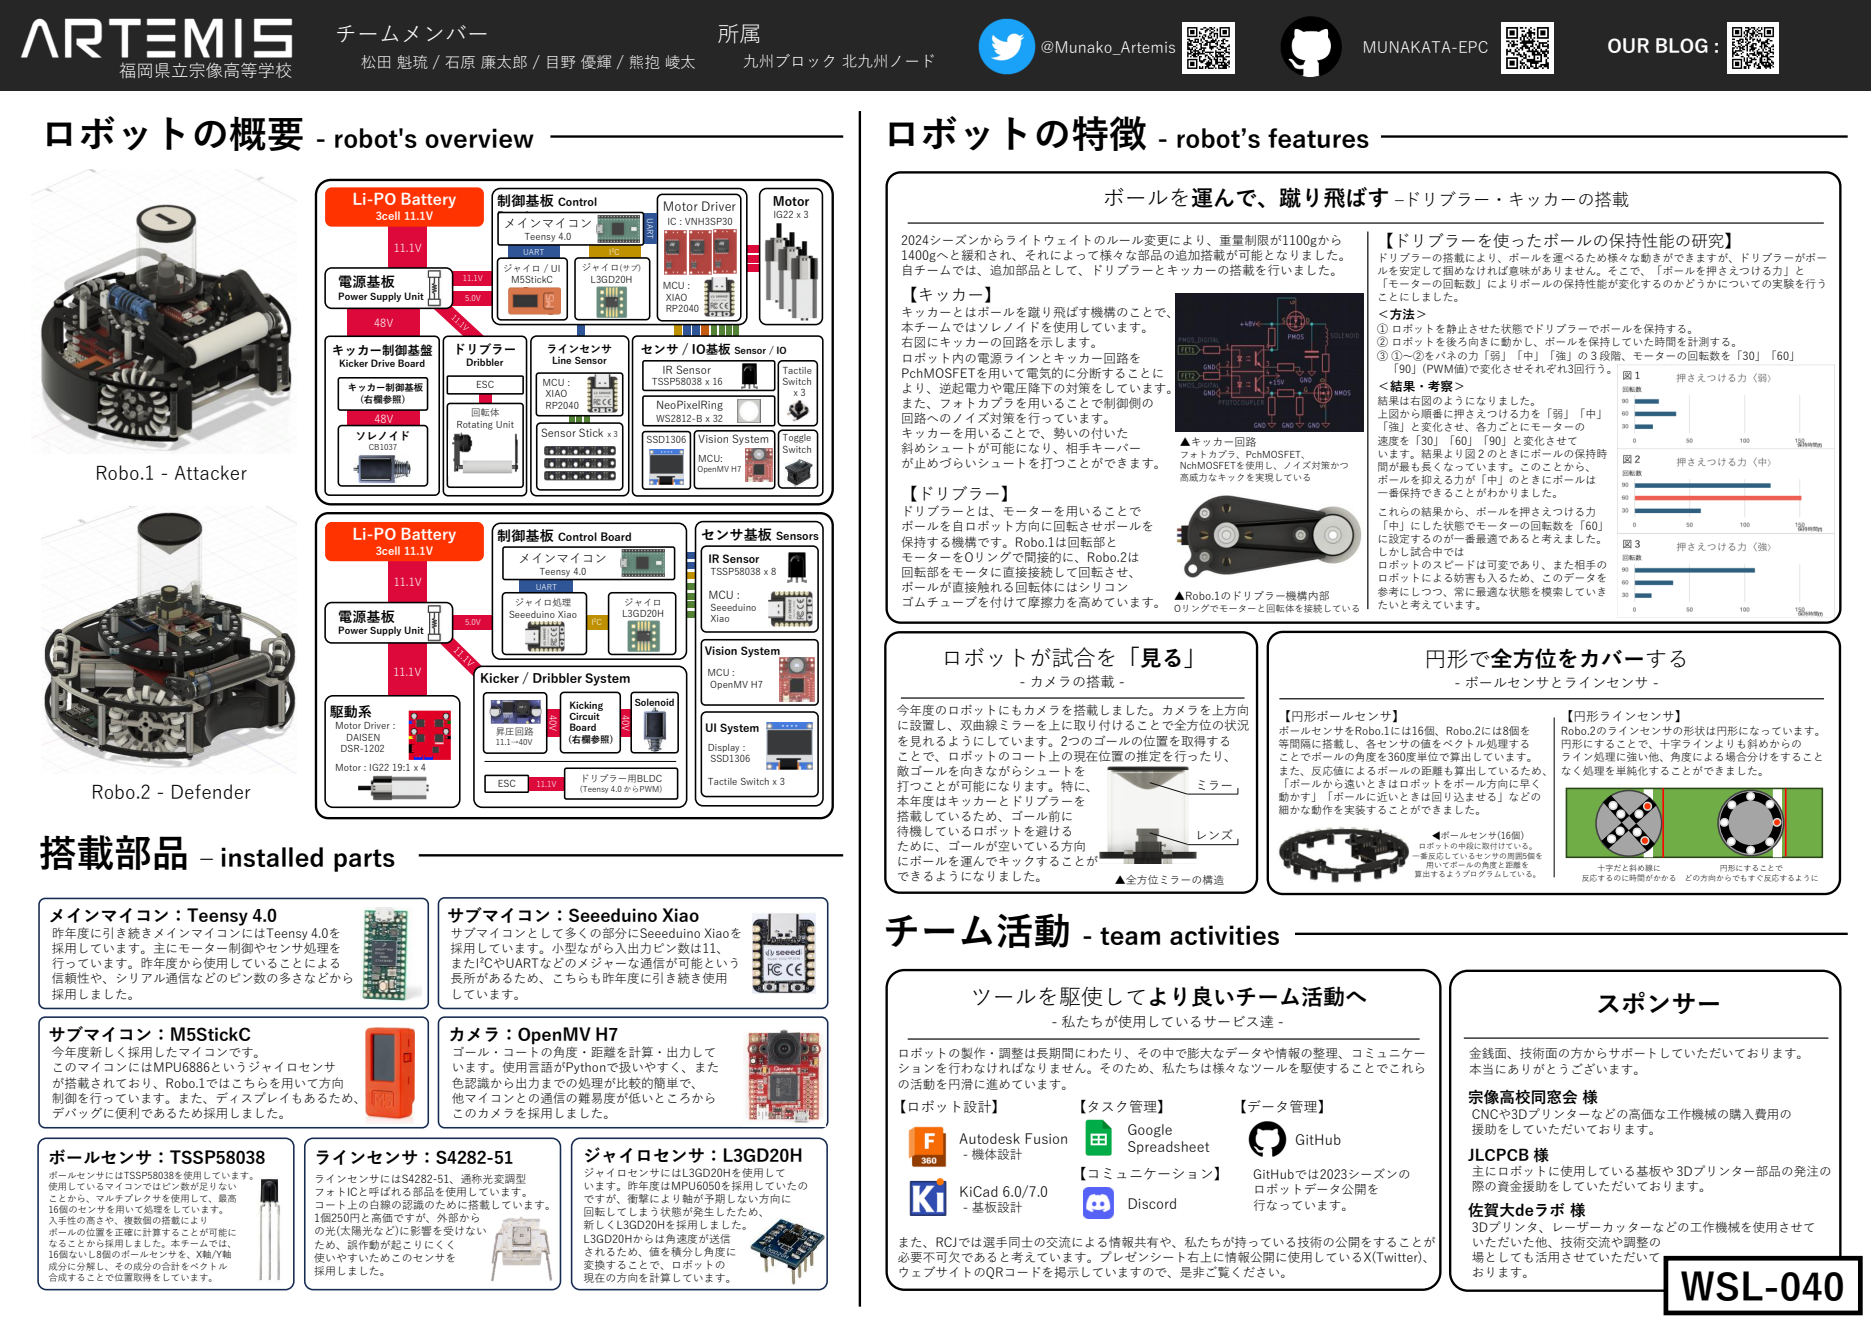
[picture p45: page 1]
Robo.2 - Defender; Motor; IR Sensor TSSP58038 x 16; SSD1306; NeoPixelRing; Vision System; MCU: OpenMV H7; ラインセンサ Line Sensor; MCU : XIAO RP2040; Sensor Stick x 3; 駆動系; Motor Driver : DAISEN DSR-1202; Motor : IG22 19:1 x 4; センサ基板 Sensors; IR Sensor TSSP58038 x 8; MCU : Seeeduino Xiao; MCU : OpenMV H7; UI System; Display : SSD1306; Tactile Switch x 3; UART; I²C; ジャイロ L3GD20H; ジャイロ処理; 電源基板; Seeeduino Xiao; 制御基板 Control; Board; ジャイロ / UI M5StickC; ジャイロ(サブ) L3GD20H; Motor Driver; IC : VNH3SP30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

松田 魁琉 / 石原 廉太郎 / 目野 優輝 / 熊抱 崚太

ロボットの概要 - robot's overview

ロボットの特徴 - robot’s features

Li-PO Battery
3cell 11.1V

ボールを運んで、蹴り飛ばす –ドリブラー・キッカーの搭載

【ドリブラーを使ったボールの保持性能の研究】
ドリブラーの搭載により、ボールを運べるため様々な動きができますが、ドリブラーがボー
ルを安定して掴めなければ意味がありません。そこで、「ボールを押さえつける力」と
「モーターの回転数」によりボールの保持性能が変化するのかどうかについての実験を行う
ことにしました。
① ロボットを静止させた状態でドリブラーでボールを保持する。
② ロボットを後ろ向きに動かし、ボールを保持していた時間を計測する。
③ ①～②をバネの力「弱」「中」「強」の３段階、モーターの回転数を「30」「60」
「90」(PWM値)で変化させそれぞれ3回行う。
結果は右図のようになりました。
上図から順番に押さえつける力を「弱」「中」
「強」と変化させ、各力ごとにモーターの
速度を「30」「60」「90」と変化させて
います。結果より図２のときにボールの保持時
間が最も長くなっています。このことから、
ボールを抑える力が「中」のときにボールは
一番保持できることがわかりました。
これらの結果から、ボールを押さえつける力
「中」にした状態でモーターの回転数を「60」

電源基板
Power Supply Unit

キッカー制御基盤
Kicker Drive Board

センサ / IO基板 Sensor / IO

・Autodesk Fusion : 機体の設計

制御基板 Control Board
メインマイコン
Teensy 4.0

Kicker / Dribbler System

今年度のロボットにもカメラを搭載しました。カメラを上方向
に設置し、双曲線ミラーを上に取り付けることで全方位の状況
を見れるようにしています。2つのゴールの位置を取得する
ことで、ロボットのコート上の現在位置の推定を行ったり、
敵ゴールを向きながらシュートを
打つことが可能になります。特に、
本年度はキッカーとドリブラーを
搭載しているため、ゴール前に
待機しているロボットを避ける
ために、ゴールが空いている方向
にボールを運んでキックすることが
チーム活動 - team activities

【円形ボールセンサ】
ボールセンサをRobo.1には16個、Robo.2には8個を
等間隔に搭載し、各センサの値をベクトル処理する
ことでボールの角度を360度単位で算出しています。
また、反応値によるボールの距離も算出しているため、
「ボールから遠いときはロボットをボール方向に早く
動かす」「ボールに近いときは回り込ませる」などの
細かな動作を実装することができました。

搭載部品 – installed parts

サブマイコン：Seeeduino Xiao
サブマイコンとして多くの部分にSeeeduino Xiaoを
採用しています。小型ながら入出力ピン数は11、
またI²CやUARTなどのメジャーな通信が可能という
長所があるため、こちらも昨年度に引き続き使用
しています。

カメラ：OpenMV H7
ゴール・コートの角度・距離を計算・出力して
います。使用言語がPythonで扱いやすく、また
色認識から出力までの処理が比較的簡単で、
他マイコンとの通信の難易度が低いところから
このカメラを採用しました。

ロボットの製作・調整は長期間にわたり、その中で膨大なデータや情報の整理、コミュニケー
ションを行わなければなりません。そのため、私たちは様々なツールを駆使することでこれら
の活動を円滑に進めています。

また、RCJでは選手同士の交流による情報共有や、私たちが持っている技術の公開をすることが
必要不可欠であると考えています。プレゼンシート右上に情報公開に使用しているX(Twitter)、
ウェブサイトのQRコードを掲示していますので、是非ご覧ください。

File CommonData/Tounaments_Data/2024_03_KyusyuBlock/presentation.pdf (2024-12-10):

# チームメンバー

# 松田 魁琉 / 目野 優輝 / 石原 廉太郎 / 熊抱 崚太

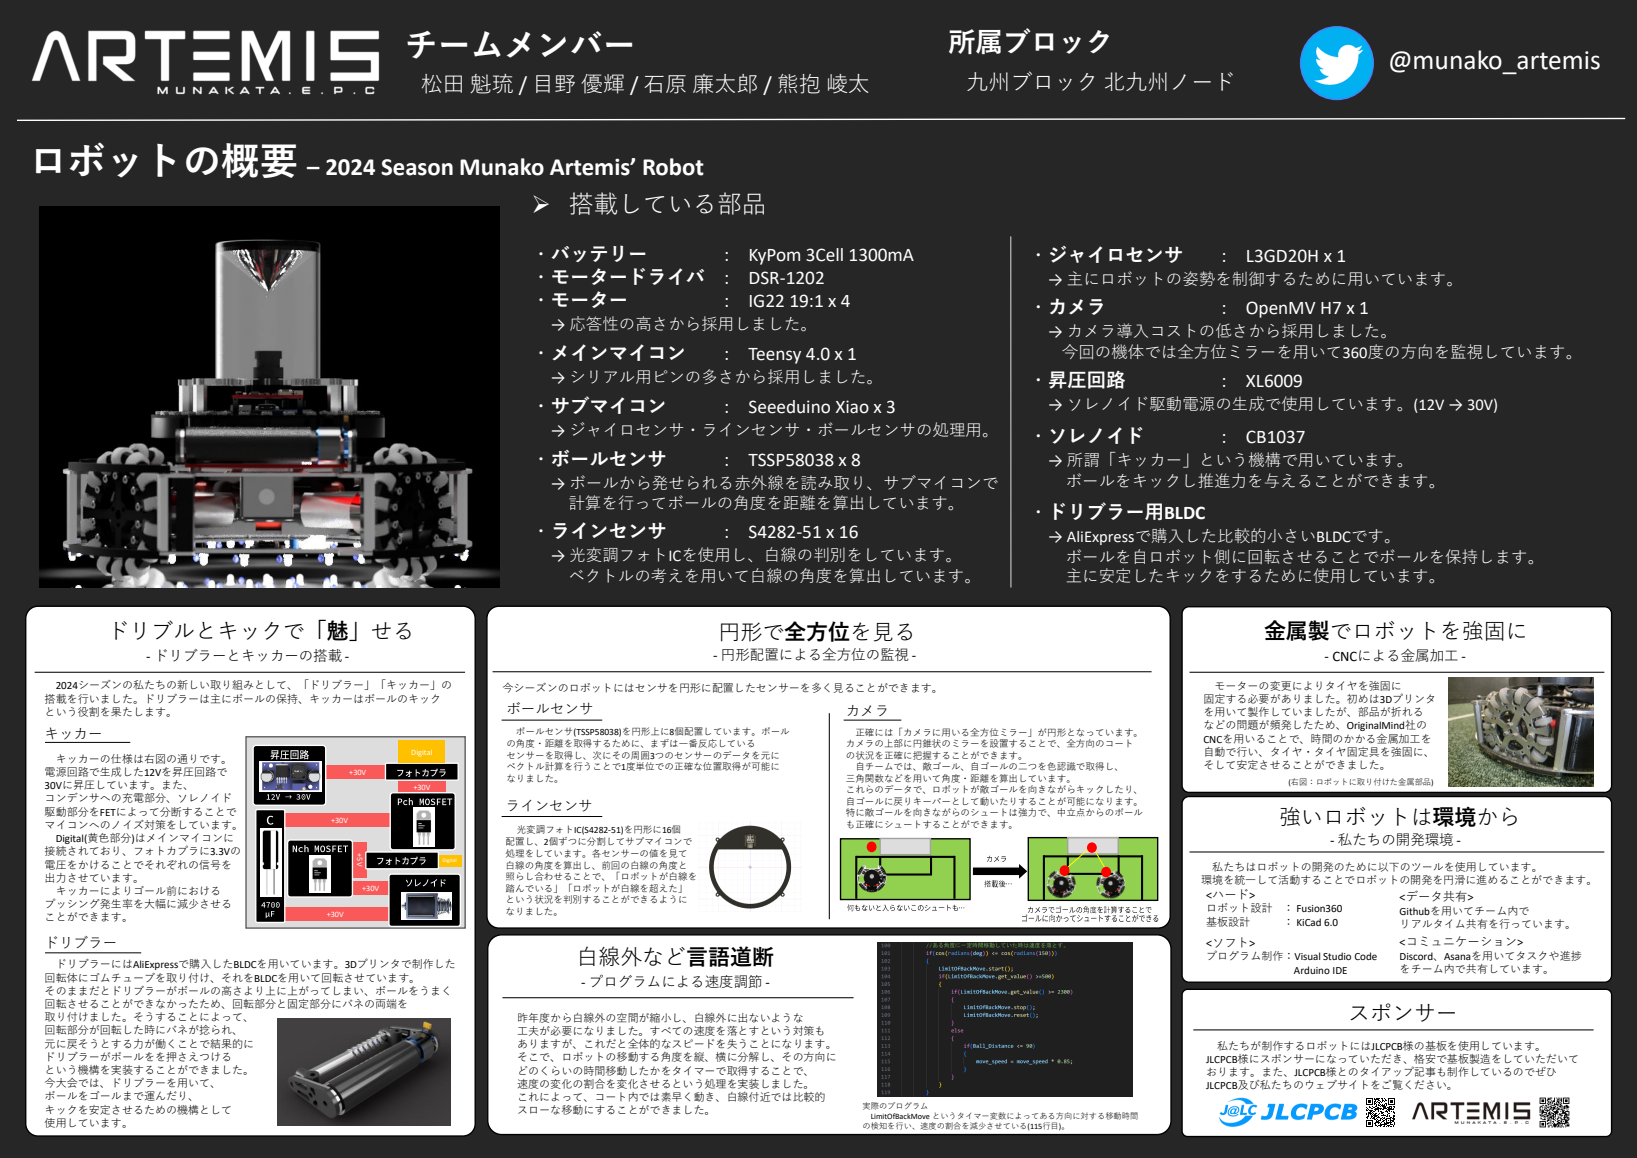
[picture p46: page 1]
所属ブロック; 九州ブロック 北九州ノード; ➢ 搭載している部品; ・バッテリー; : KyPom 3Cell 1300mA; ・モーター; ・メインマイコン; : Teensy 4.0 x 1; ・サブマイコン; : Seeeduino Xiao x 3; ・ボールセンサ; : TSSP58038 x 8; ・ラインセンサ; @munako_artemis; ・ジャイロセンサ; → 主にロボットの姿勢を制御するために用いています。; ・カメラ; : OpenMV H7 x 1; → カメラ導入コストの低さから採用しました。 今回の機体では全方位ミラーを用いて360度の方向を監視しています。; ・昇圧回路; → ソレノイド駆動電源の生成で使用しています。(12V → 30V); ・ソレノイド; → 所謂「キッカー」という機構で用いています。 ボールをキックし推進力を与えることができます。; ・ドリブラー用BLDC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

ロボットの概要 – 2024 Season Munako Artemis’ Robot

・モータードライバ : DSR-1202
→ 応答性の高さから採用しました。
→ シリアル用ピンの多さから採用しました。
→ ジャイロセンサ・ラインセンサ・ボールセンサの処理用。
→ ボールから発せられる赤外線を読み取り、サブマイコンで
計算を行ってボールの角度を距離を算出しています。
→ 光変調フォトICを使用し、白線の判別をしています。
ベクトルの考えを用いて白線の角度を算出しています。

2024シーズンの私たちの新しい取り組みとして、「ドリブラー」「キッカー」の
搭載を行いました。ドリブラーは主にボールの保持、キッカーはボールのキック
という役割を果たします。
キッカー

モーターの変更によりタイヤを強固に
固定する必要がありました。初めは3Dプリンタ
を用いて製作していましたが、部品が折れる
などの問題が頻発したため、OriginalMind社の
CNCを用いることで、時間のかかる金属加工を
自動で行い、タイヤ・タイヤ固定具を強固に、
そして安定させることができました。

正確には「カメラに用いる全方位ミラー」が円形となっています。
カメラの上部に円錐状のミラーを設置することで、全方向のコート
の状況を正確に把握することができます。
自チームでは、敵ゴール、自ゴールの二つを色認識で取得し、
三角関数などを用いて角度・距離を算出しています。
これらのデータで、ロボットが敵ゴールを向きながらキックしたり、
自ゴールに戻りキーパーとして動いたりすることが可能になります。
特に敵ゴールを向きながらのシュートは強力で、中立点からのボール
も正確にシュートすることができます。

私たちはロボットの開発のために以下のツールを使用しています。
環境を統一して活動することでロボットの開発を円滑に進めることができます。
<ハード>
ロボット設計 ： Fusion360
<ソフト>
プログラム制作：Visual Studio Code

昨年度から白線外の空間が縮小し、白線外に出ないような
工夫が必要になりました。すべての速度を落とすという対策も
ありますが、これだと全体的なスピードを失うことになります。
そこで、ロボットの移動する角度を縦、横に分解し、その方向に
どのくらいの時間移動したかをタイマーで取得することで、
速度の変化の割合を変化させるという処理を実装しました。
これによって、コート内では素早く動き、白線付近では比較的

私たちが制作するロボットにはJLCPCB様の基板を使用しています。
JLCPCB様にスポンサーになっていただき、格安で基板製造をしていただいて
おります。また、JLCPCB様とのタイアップ記事も制作しているのでぜひ
JLCPCB及び私たちのウェブサイトをご覧ください。

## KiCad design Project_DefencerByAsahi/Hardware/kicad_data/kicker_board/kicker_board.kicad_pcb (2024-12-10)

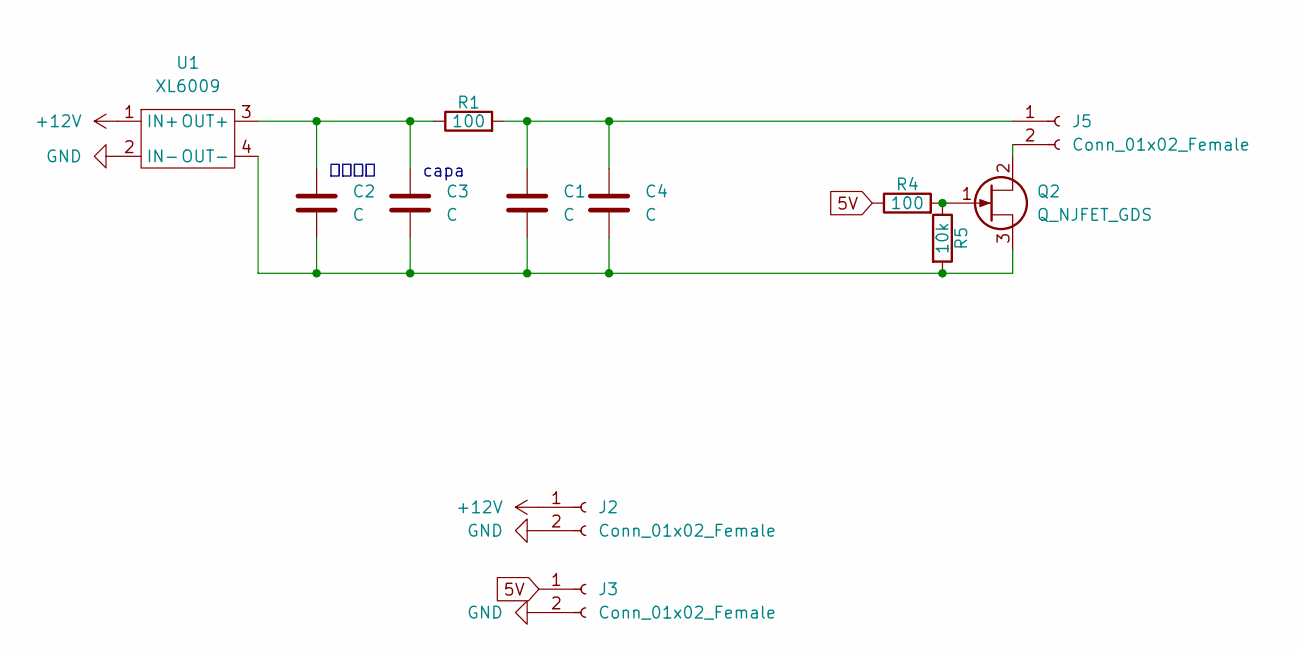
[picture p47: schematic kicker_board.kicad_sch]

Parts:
C1, C4: C; C_Radial_D16.0mm_H31.5mm_P7.50mm
C2: C; C_Disc_D8.0mm_W2.5mm_P5.00mm
C3: C; C_Radial_D12.5mm_H20.0mm_P5.00mm
J2, J3, J5: Conn_01x02_Female; PinSocket_1x02_P2.54mm_Vertical
Q2: Q_NJFET_GDS; FET(big)
R1, R4: 100; R_Axial_DIN0204_L3.6mm_D1.6mm_P7.62mm_Horizontal
R5: 10k; R_Axial_DIN0204_L3.6mm_D1.6mm_P7.62mm_Horizontal
U1: XL6009

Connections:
5V: J3.1, R4.1
+12V: J2.1, U1.1 (IN+)
GND: J2.2, J3.2, U1.2 (IN-)
unnamed: C1.1, C4.1, J5.1, R1.2
unnamed: C1.2, C2.2, C3.2, C4.2, Q2.3 (S), R5.2, U1.4 (OUT-)
unnamed: C2.1, C3.1, R1.1, U1.3 (OUT+)
unnamed: J5.2, Q2.2 (D)
unnamed: Q2.1 (G), R4.2, R5.1

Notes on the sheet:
セラコン
capa

Board: 2 copper layers, 12 parts (1 on the bottom side), 8 nets, no tracks yet.

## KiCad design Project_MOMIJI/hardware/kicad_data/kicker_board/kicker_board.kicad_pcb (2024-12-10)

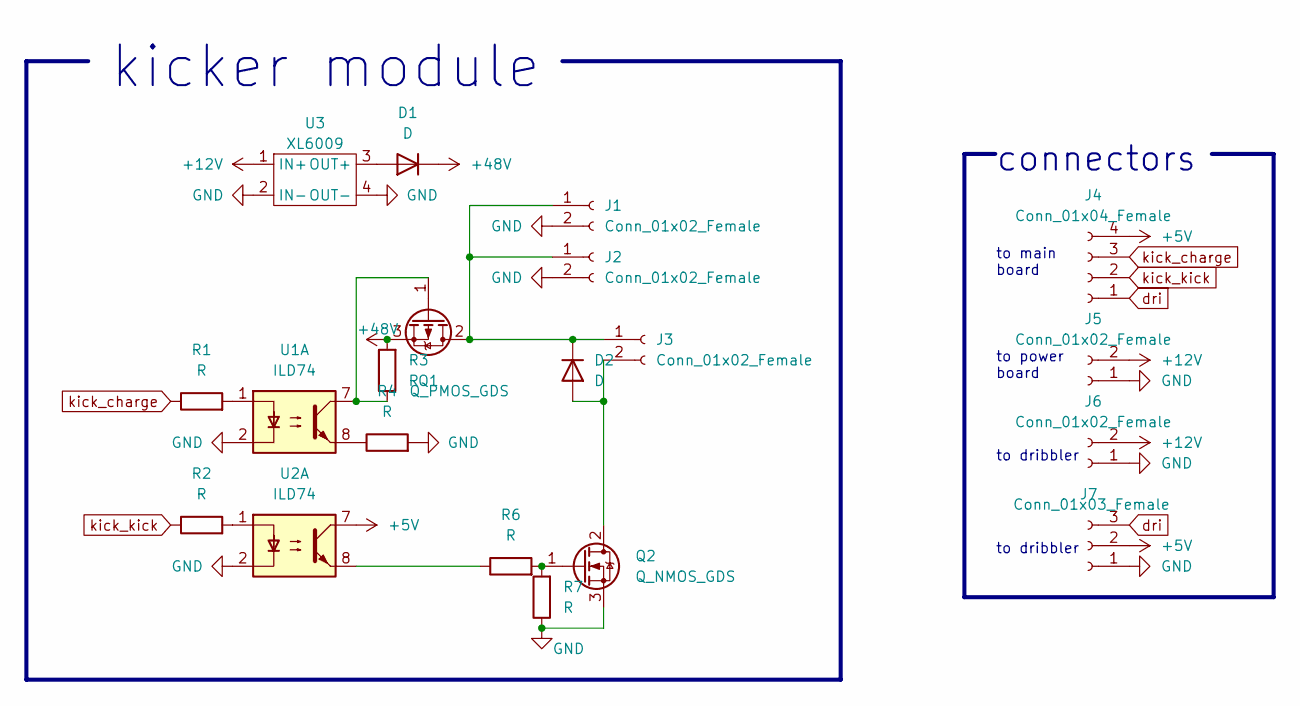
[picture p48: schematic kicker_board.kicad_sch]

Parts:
D1, D2: D; D_5W_P12.70mm_Horizontal
J1, J2, J3, J5, J6: Conn_01x02_Female; JST_XH_B2B-XH-A_1x02_P2.50mm_Vertical
J4: Conn_01x04_Female; JST_XH_B4B-XH-A_1x04_P2.50mm_Vertical
J7: Conn_01x03_Female; JST_XH_B3B-XH-A_1x03_P2.50mm_Vertical
Q1: Q_PMOS_GDS; Pch MOSFET
Q2: Q_NMOS_GDS; Pch MOSFET
R1, R2, R3, R4, R6, R7: R; R_Axial_DIN0207_L6.3mm_D2.5mm_P7.62mm_Horizontal
U1, U2: ILD74; フォトカプラー
U3: XL6009

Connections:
+5V: J4.4, J7.2, U2.7
+12V: J5.2, J6.2, U3.1 (IN+)
+48V: D1.1 (K), Q1.3 (S), R3.2
GND: J1.2, J2.2, J5.1, J6.1, J7.1, Q2.3 (S), R4.2, R7.1, U1.2, U2.2, U3.2 (IN-), U3.4 (OUT-)
unnamed: D1.2 (A), U3.3 (OUT+)
unnamed: D2.1 (K), J1.1, J2.1, J3.1, Q1.2 (D)
unnamed: D2.2 (A), J3.2, Q2.2 (D)
unnamed: Q1.1 (G), R3.1, U1.7
unnamed: Q2.1 (G), R6.2, R7.2
unnamed: R1.2, U1.1
unnamed: R2.2, U2.1
unnamed: R4.1, U1.8
unnamed: R6.1, U2.8
dri: J4.1, J7.3
kick_charge: J4.3, R1.1
kick_kick: J4.2, R2.1

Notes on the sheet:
to dribbler
kicker module
to main board
connectors
to power board

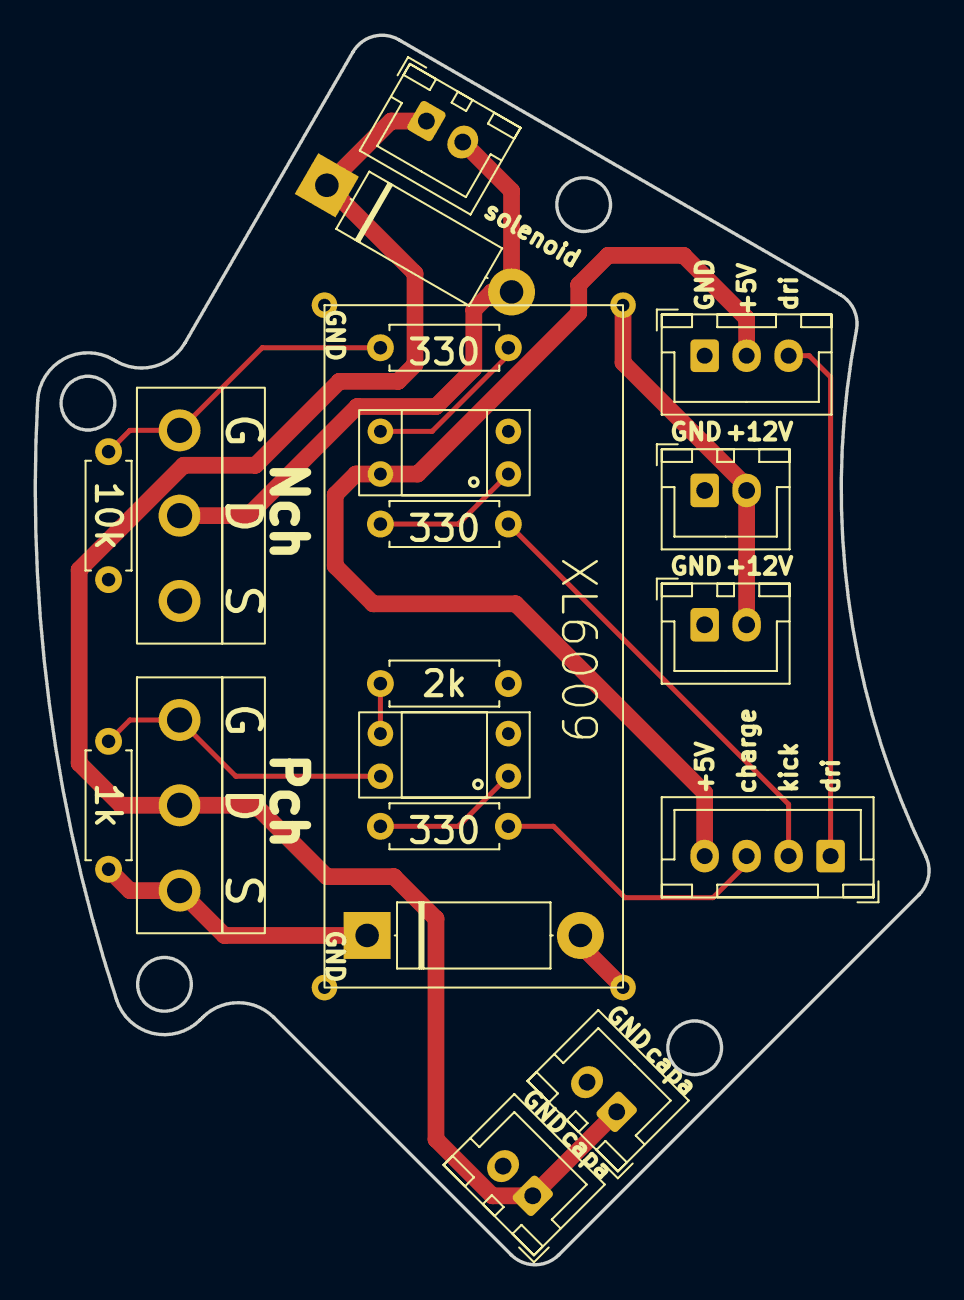
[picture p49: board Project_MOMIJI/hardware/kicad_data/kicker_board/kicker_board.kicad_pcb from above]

Board: 2 copper layers, 53.2 x 73.2 mm, 20 parts (0 on the bottom side), 16 nets.

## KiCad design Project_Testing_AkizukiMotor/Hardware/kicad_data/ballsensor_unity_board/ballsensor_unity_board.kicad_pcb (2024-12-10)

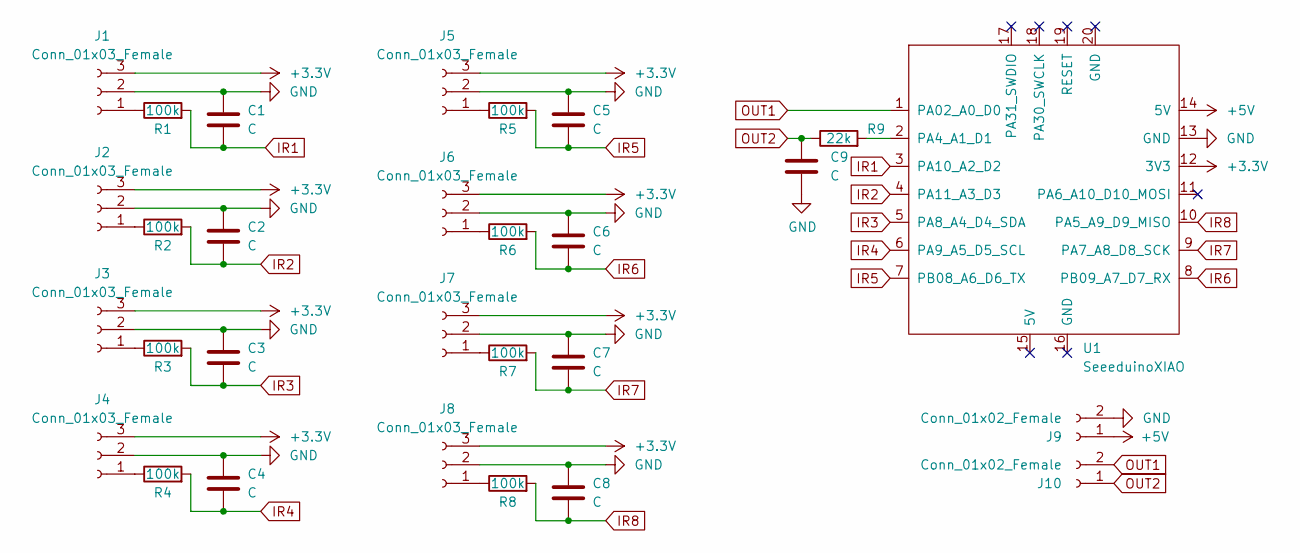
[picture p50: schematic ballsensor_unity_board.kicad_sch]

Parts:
C1, C2, C3, C4, C5, C6, C7, C8, C9: C; C_Disc_D5.0mm_W2.5mm_P5.00mm
J1, J2, J3, J4, J5, J6, J7, J8: Conn_01x03_Female; PinSocket_1x03_P2.54mm_Vertical
J9, J10: Conn_01x02_Female; PinSocket_1x02_P2.54mm_Vertical
R1, R2, R3, R4, R5, R6, R7, R8: 100k; R_Axial_DIN0204_L3.6mm_D1.6mm_P5.08mm_Horizontal
R9: 22k; R_Axial_DIN0204_L3.6mm_D1.6mm_P5.08mm_Horizontal
U1: SeeeduinoXIAO; seeeduinoXIAO

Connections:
+3.3V: J1.3, J2.3, J3.3, J4.3, J5.3, J6.3, J7.3, J8.3, U1.12 (3V3)
+5V: J9.1, U1.14 (5V)
GND: C1.1, C2.1, C3.1, C4.1, C5.1, C6.1, C7.1, C8.1, C9.2, J1.2, J2.2, J3.2, J4.2, J5.2, J6.2, J7.2, J8.2, J9.2, U1.13 (GND)
IR1: C1.2, R1.2, U1.3 (PA10_A2_D2)
IR2: C2.2, R2.2, U1.4 (PA11_A3_D3)
IR3: C3.2, R3.2, U1.5 (PA8_A4_D4_SDA)
IR4: C4.2, R4.2, U1.6 (PA9_A5_D5_SCL)
IR5: C5.2, R5.2, U1.7 (PB08_A6_D6_TX)
IR6: C6.2, R6.2, U1.8 (PB09_A7_D7_RX)
IR7: C7.2, R7.2, U1.9 (PA7_A8_D8_SCK)
IR8: C8.2, R8.2, U1.10 (PA5_A9_D9_MISO)
unnamed: J1.1, R1.1
unnamed: J2.1, R2.1
unnamed: J3.1, R3.1
unnamed: J4.1, R4.1
unnamed: J5.1, R5.1
unnamed: J6.1, R6.1
unnamed: J7.1, R7.1
unnamed: J8.1, R8.1
unnamed: R9.2, U1.2 (PA4_A1_D1)
OUT1: J10.2, U1.1 (PA02_A0_D0)
OUT2: C9.1, J10.1, R9.1

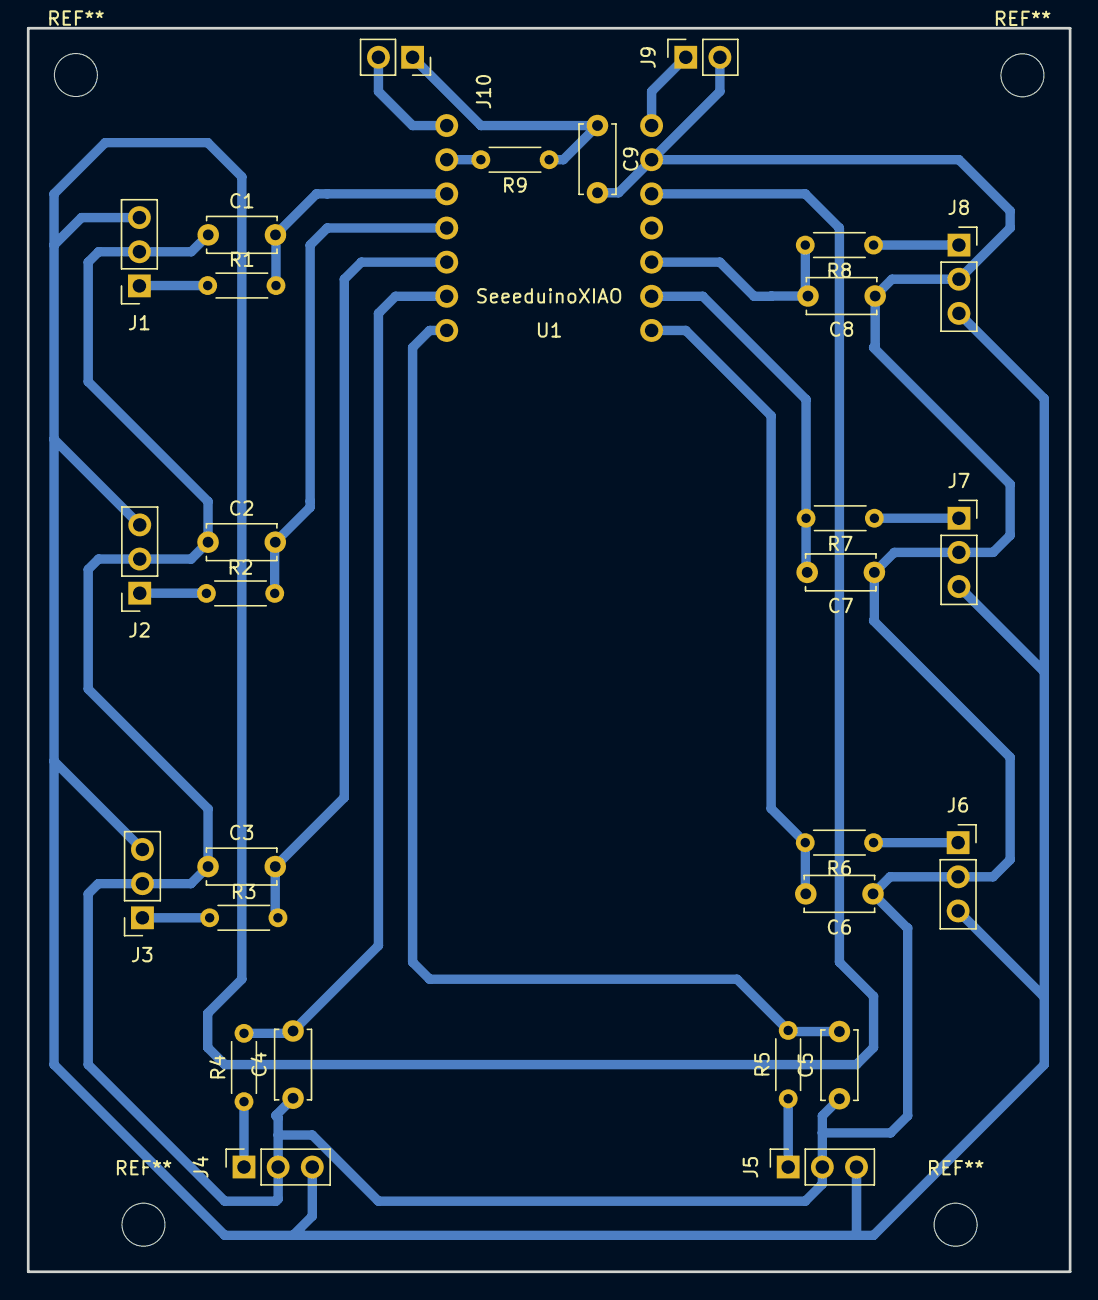
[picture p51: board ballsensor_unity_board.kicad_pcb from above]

Board: 2 copper layers, 77.5 x 92.5 mm, 29 parts (0 on the bottom side), 22 nets.

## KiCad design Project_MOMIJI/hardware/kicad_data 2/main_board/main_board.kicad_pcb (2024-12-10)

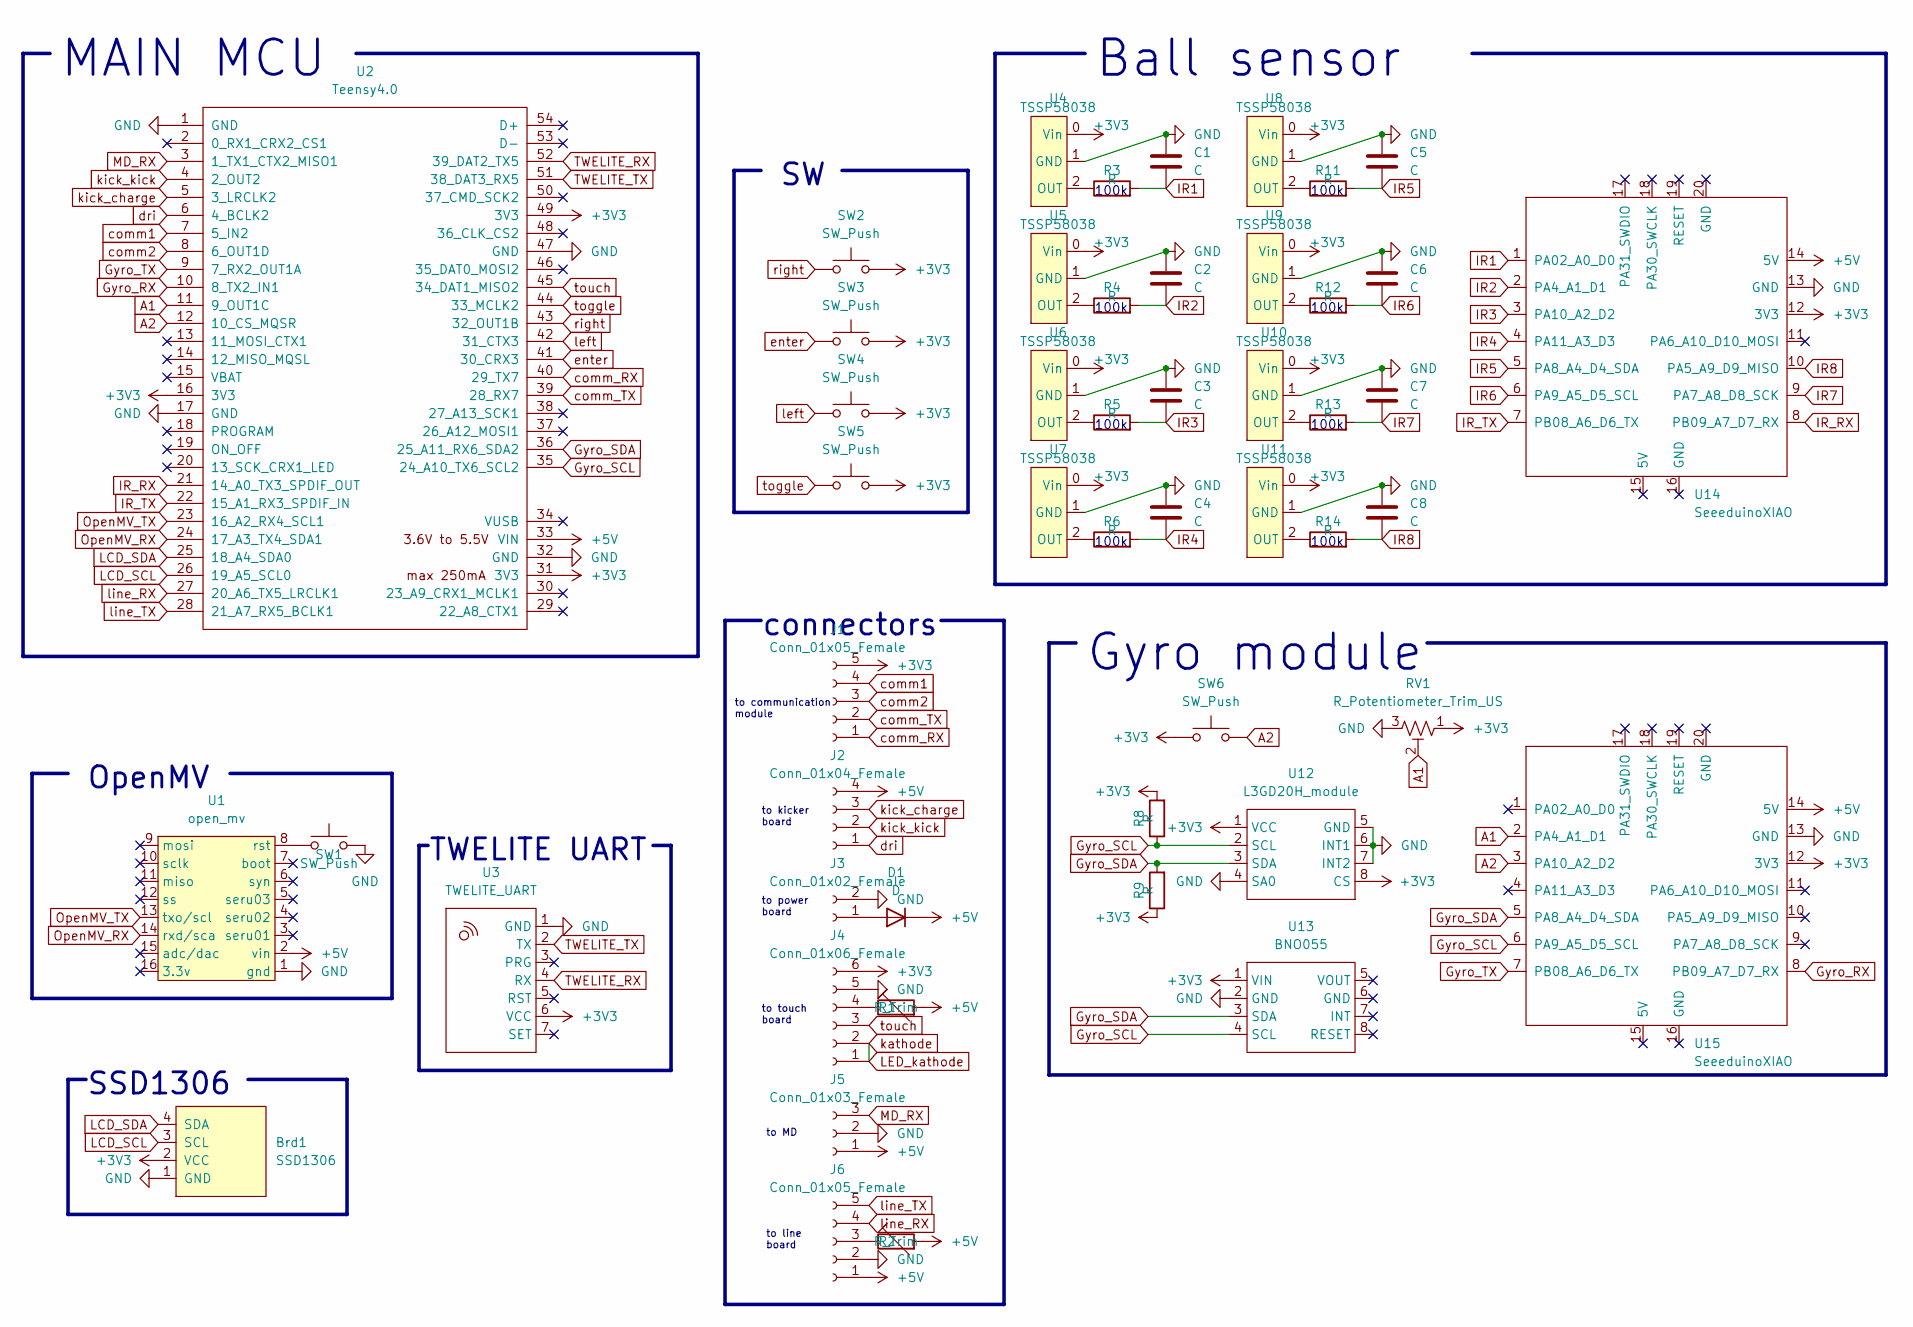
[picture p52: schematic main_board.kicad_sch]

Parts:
Brd1: SSD1306; PinSocket_1x04_P2.54mm_Vertical
C1, C2, C3, C4, C5, C6, C7, C8: C; C_Disc_D3.4mm_W2.1mm_P2.50mm
D1: D; D_5W_P12.70mm_Horizontal
J1, J6: Conn_01x05_Female; JST_XH_B5B-XH-A_1x05_P2.50mm_Vertical
J2: Conn_01x04_Female; JST_XH_B4B-XH-A_1x04_P2.50mm_Vertical
J3: Conn_01x02_Female; JST_XH_B2B-XH-A_1x02_P2.50mm_Vertical
J4: Conn_01x06_Female; JST_XH_B6B-XH-A_1x06_P2.50mm_Vertical
J5: Conn_01x03_Female; JST_XH_B3B-XH-A_1x03_P2.50mm_Vertical
R1, R2: R_Trim; 可変抵抗
R3, R4, R5, R6, R8, R9, R11, R12, R13, R14: R; R_Axial_DIN0207_L6.3mm_D2.5mm_P7.62mm_Horizontal
RV1: R_Potentiometer_Trim_US; 可変抵抗
SW1, SW2, SW3, SW4: SW_Push; SW_PUSH_6mm_H7.3mm
SW5: SW_Push; PinHeader_1x02_P2.54mm_Vertical
SW6: SW_Push; SW
U1: open_mv; OpenMV
U2: Teensy4.0; Teensy_Brakeout
U3: TWELITE_UART; TWELITE UART
U4, U5, U6, U7, U8, U9, U10, U11: TSSP58038
U12: L3GD20H_module; L3GD20H_Module_KiCad6.0
U13: BNO055
U14, U15: SeeeduinoXIAO; seeeduinoXIAO

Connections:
+3V3: Brd1.2 (VCC), J1.5, J4.6, R8.2, R9.1, RV1.1, SW2.2, SW3.2, SW4.2, SW5.2, SW6.1, U2.16 (3V3), U2.31 (3V3), U2.49 (3V3), U3.6 (VCC), U4.0 (Vin), U5.0 (Vin), U6.0 (Vin), U7.0 (Vin), U8.0 (Vin), U9.0 (Vin), U10.0 (Vin), U11.0 (Vin), U12.1 (VCC), U12.8 (CS), U13.1 (VIN), U14.12 (3V3), U15.12 (3V3)
+5V: D1.1 (K), J2.4, J5.1, J6.1, R1.2, R2.2, U1.2 (vin), U2.33 (VIN), U14.14 (5V), U15.14 (5V)
A1: RV1.2, U2.11 (9_OUT1C), U15.2 (PA4_A1_D1)
A2: SW6.2, U2.12 (10_CS_MQSR), U15.3 (PA10_A2_D2)
GND: Brd1.1 (GND), C1.1, C2.1, C3.1, C4.1, C5.1, C6.1, C7.1, C8.1, J3.2, J4.5, J5.2, J6.2, RV1.3, SW1.2, U1.1 (gnd), U2.1 (GND), U2.17 (GND), U2.32 (GND), U2.47 (GND), U3.1 (GND), U4.1 (GND), U5.1 (GND), U6.1 (GND), U7.1 (GND), U8.1 (GND), U9.1 (GND), U10.1 (GND), U11.1 (GND), U12.4 (SA0), U12.5 (GND), U12.6 (INT1), U12.7 (INT2), U13.2 (GND), U14.13 (GND), U15.13 (GND)
Gyro_RX: U2.10 (8_TX2_IN1), U15.8 (PB09_A7_D7_RX)
Gyro_SCL: R8.1, U2.35 (24_A10_TX6_SCL2), U12.2 (SCL), U13.4 (SCL), U15.6 (PA9_A5_D5_SCL)
Gyro_SDA: R9.2, U2.36 (25_A11_RX6_SDA2), U12.3 (SDA), U13.3 (SDA), U15.5 (PA8_A4_D4_SDA)
Gyro_TX: U2.9 (7_RX2_OUT1A), U15.7 (PB08_A6_D6_TX)
IR1: C1.2, R3.2, U14.1 (PA02_A0_D0)
IR2: C2.2, R4.2, U14.2 (PA4_A1_D1)
IR3: C3.2, R5.2, U14.3 (PA10_A2_D2)
IR4: C4.2, R6.2, U14.4 (PA11_A3_D3)
IR5: C5.2, R11.2, U14.5 (PA8_A4_D4_SDA)
IR6: C6.2, R12.2, U14.6 (PA9_A5_D5_SCL)
IR7: C7.2, R13.2, U14.9 (PA7_A8_D8_SCK)
IR8: C8.2, R14.2, U14.10 (PA5_A9_D9_MISO)
IR_RX: U2.21 (14_A0_TX3_SPDIF_OUT), U14.8 (PB09_A7_D7_RX)
IR_TX: U2.22 (15_A1_RX3_SPDIF_IN), U14.7 (PB08_A6_D6_TX)
LCD_SCL: Brd1.3 (SCL), U2.26 (19_A5_SCL0)
LCD_SDA: Brd1.4 (SDA), U2.25 (18_A4_SDA0)
LED_kathode: J4.1, J4.2
MD_RX: J5.3, U2.3 (1_TX1_CTX2_MISO1)
unnamed: D1.2 (A), J3.1
unnamed: J4.4, R1.1
unnamed: J6.3, R2.1
unnamed: R3.1, U4.2 (OUT)
unnamed: R4.1, U5.2 (OUT)
unnamed: R5.1, U6.2 (OUT)
unnamed: R6.1, U7.2 (OUT)
unnamed: R11.1, U8.2 (OUT)
unnamed: R12.1, U9.2 (OUT)
unnamed: R13.1, U10.2 (OUT)
unnamed: R14.1, U11.2 (OUT)
unnamed: SW1.1, U1.8 (rst)
OpenMV_RX: U1.14 (rxd/sca), U2.24 (17_A3_TX4_SDA1)
OpenMV_TX: U1.13 (txo/scl), U2.23 (16_A2_RX4_SCL1)
TWELITE_RX: U2.52 (39_DAT2_TX5), U3.4 (RX)
TWELITE_TX: U2.51 (38_DAT3_RX5), U3.2 (TX)
comm1: J1.4, U2.7 (5_IN2)
comm2: J1.3, U2.8 (6_OUT1D)
comm_RX: J1.1, U2.40 (29_TX7)
comm_TX: J1.2, U2.39 (28_RX7)
dri: J2.1, U2.6 (4_BCLK2)
enter: SW3.1, U2.41 (30_CRX3)
kick_charge: J2.3, U2.5 (3_LRCLK2)
kick_kick: J2.2, U2.4 (2_OUT2)
left: SW4.1, U2.42 (31_CTX3)
line_RX: J6.4, U2.27 (20_A6_TX5_LRCLK1)
line_TX: J6.5, U2.28 (21_A7_RX5_BCLK1)
right: SW2.1, U2.43 (32_OUT1B)
toggle: SW5.1, U2.44 (33_MCLK2)
touch: J4.3, U2.45 (34_DAT1_MISO2)

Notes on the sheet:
100k
connectors
to MD
TWELITE UART
to kicker board
to power board
to communication module
to line board
SSD1306
OpenMV
Gyro module
Ball sensor
MAIN MCU
to touch board

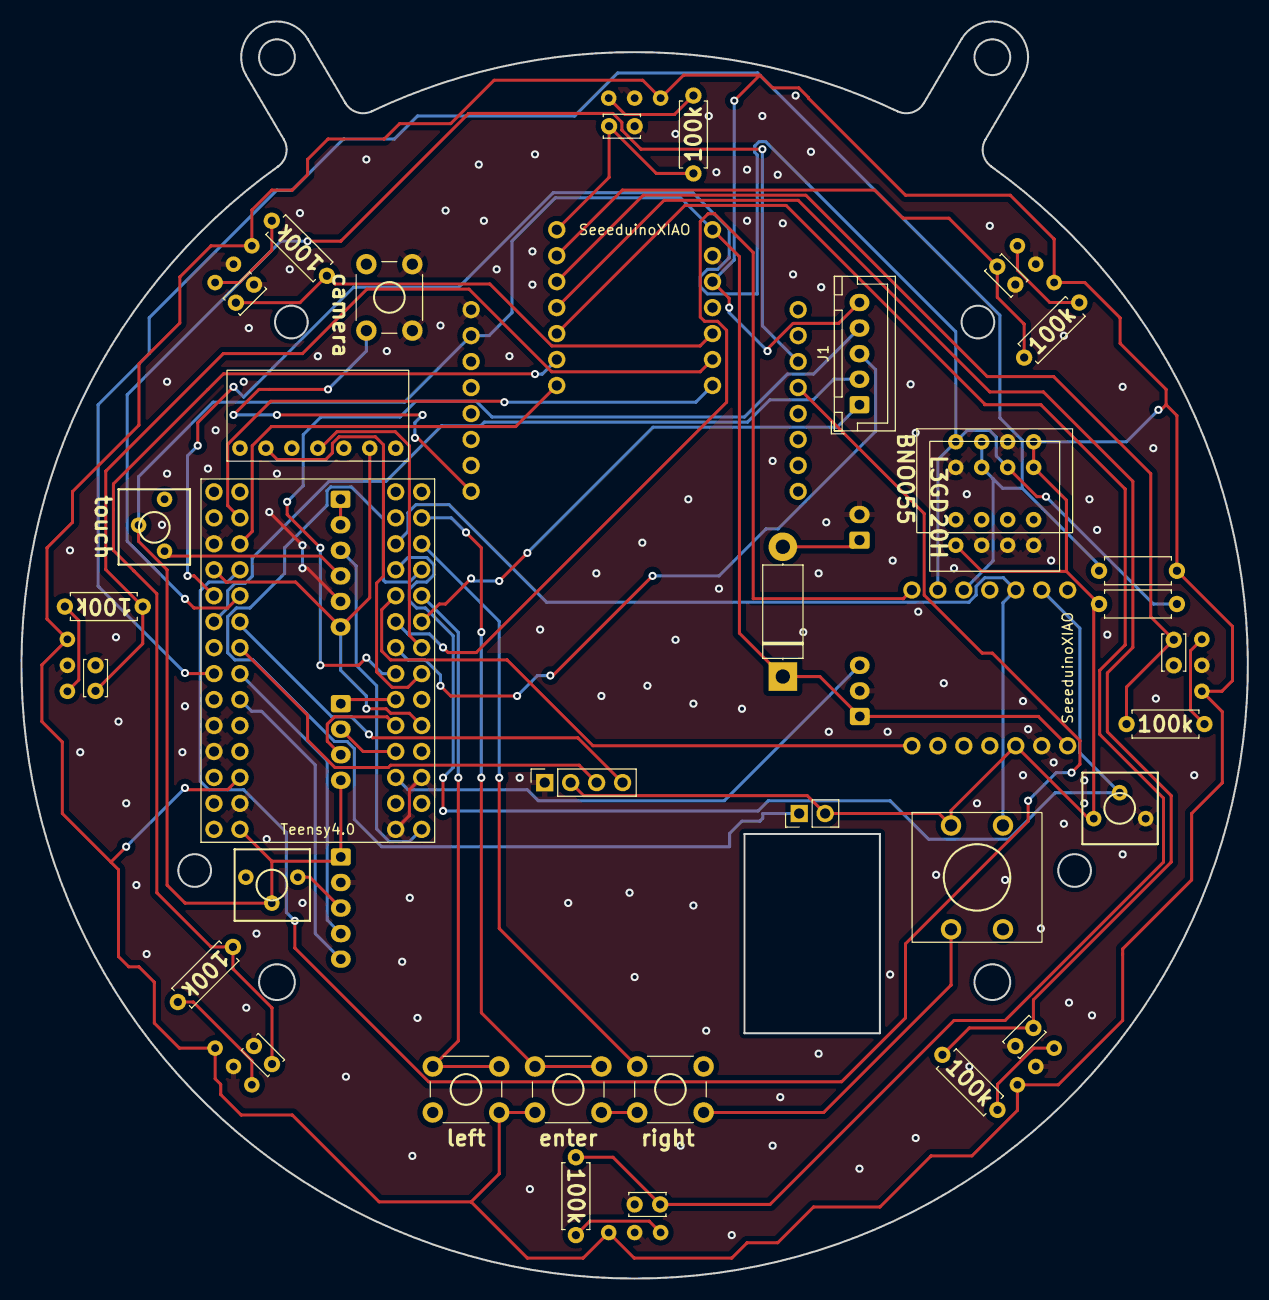
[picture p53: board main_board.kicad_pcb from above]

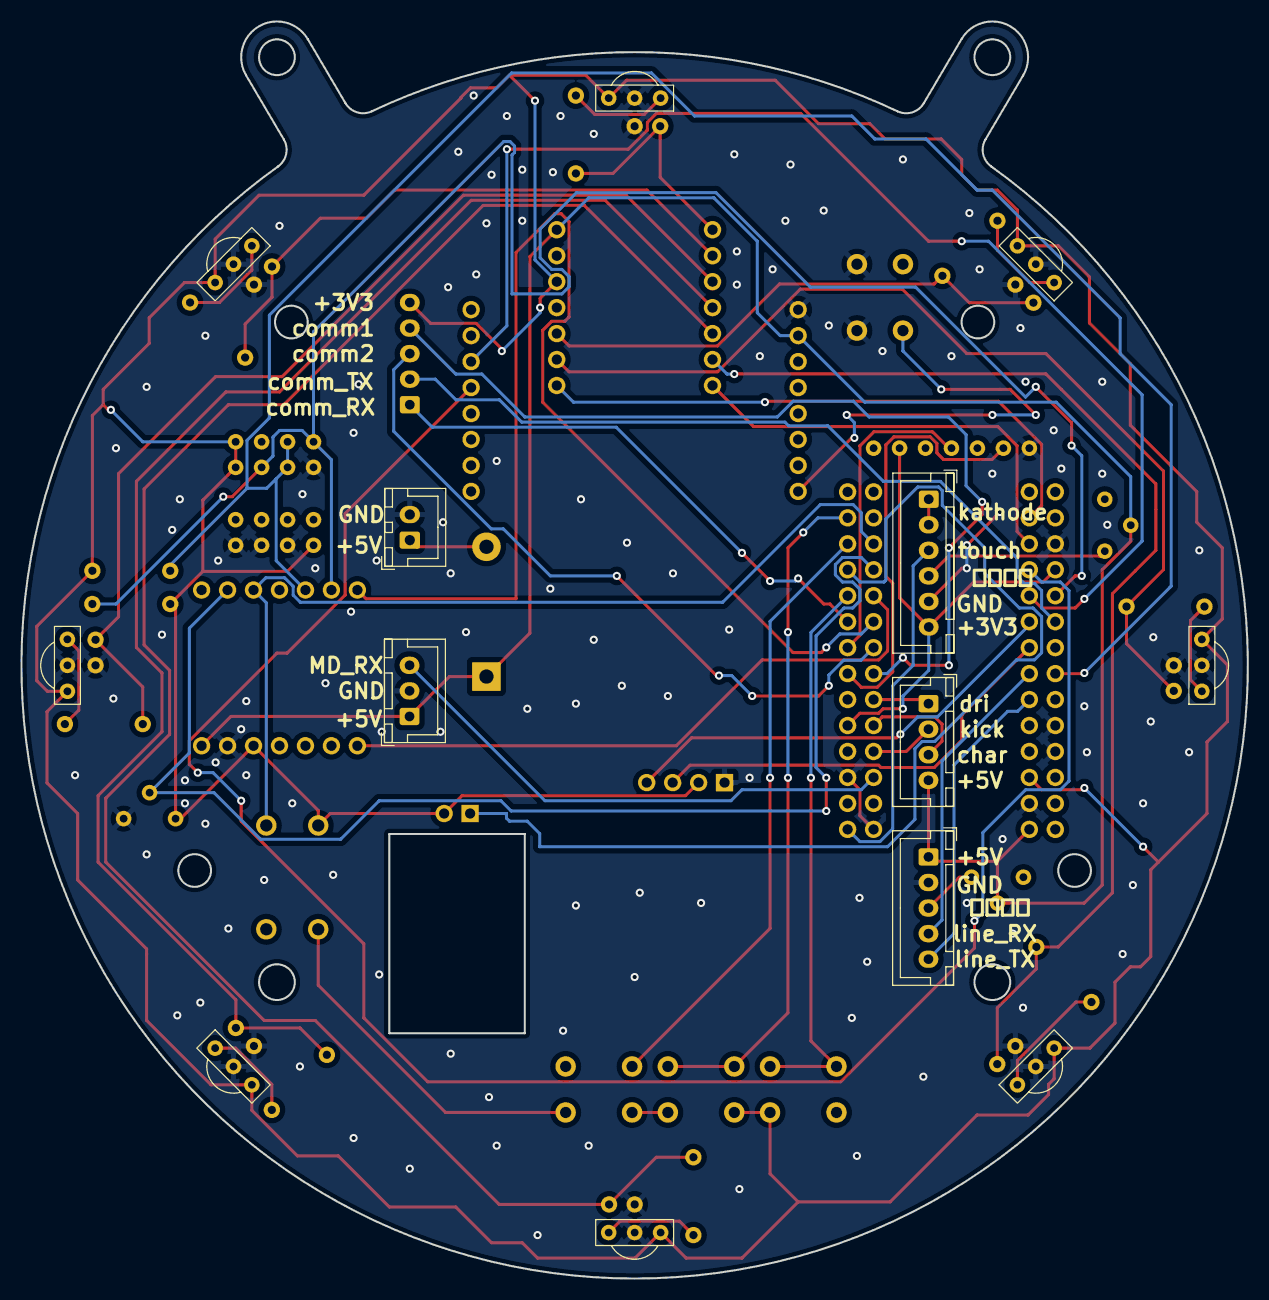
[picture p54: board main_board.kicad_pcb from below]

Board: 2 copper layers, 120.0 x 123.0 mm, 50 parts (14 on the bottom side), 53 nets.

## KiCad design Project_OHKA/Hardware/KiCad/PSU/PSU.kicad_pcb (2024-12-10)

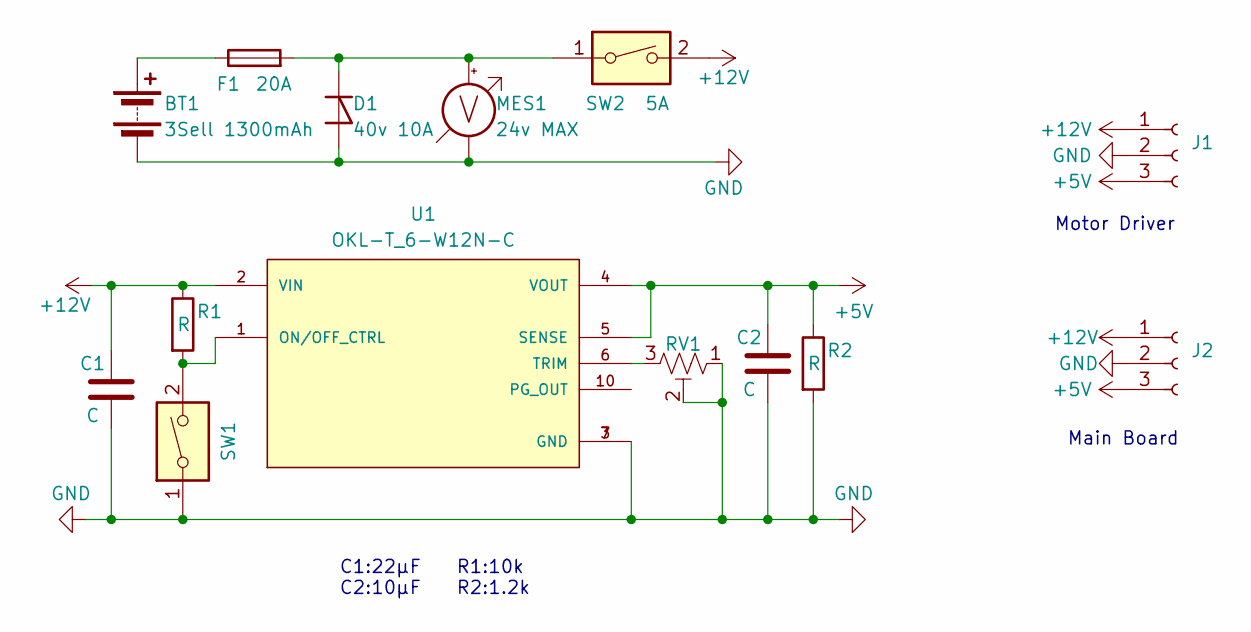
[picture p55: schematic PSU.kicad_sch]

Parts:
BT1: 3Sell 1300mAh; JST_VH_B2P-VH_1x02_P3.96mm_Vertical
C1, C2: C; C_Disc_D6.0mm_W4.4mm_P5.00mm
D1: 40v 10A; D_DO-27_P12.70mm_Horizontal
F1: 20A; fuse_socket
J1, J2: Conn_01x03_Socket; JST_XH_B3B-XH-A_1x03_P2.50mm_Vertical
MES1: 24v MAX; PinHeader_1x02_P2.54mm_Vertical
R1, R2: R; R_Axial_DIN0204_L3.6mm_D1.6mm_P5.08mm_Horizontal
RV1: R_Potentiometer_Trim_US; Potentiometer_Bourns_3296W_Vertical
SW1: 2MS1T2B4M2QES
SW2: 5A; DS-850k
U1: OKL-T_6-W12N-C; DCDC-murata-6A

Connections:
+5V: C2.1, J1.3, J2.3, R2.1, U1.4 (VOUT), U1.5 (SENSE)
+12V: C1.1, J1.1, J2.1, R1.1, SW2.2, U1.2 (VIN)
GND: BT1.2 (-), C1.2, C2.2, D1.2 (A), J1.2, J2.2, MES1.1 (-), R2.2, RV1.1, RV1.2, SW1.1, U1.3 (GND), U1.7 (GND)
unnamed: BT1.1 (+), F1.1
unnamed: D1.1 (K), F1.2, MES1.2 (+), SW2.1
unnamed: R1.2, SW1.2, U1.1 (ON/OFF_CTRL)
unnamed: RV1.3, U1.6 (TRIM)

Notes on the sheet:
Motor Driver
C1:22μF C2:10μF
R1:10k R2:1.2k
Main Board

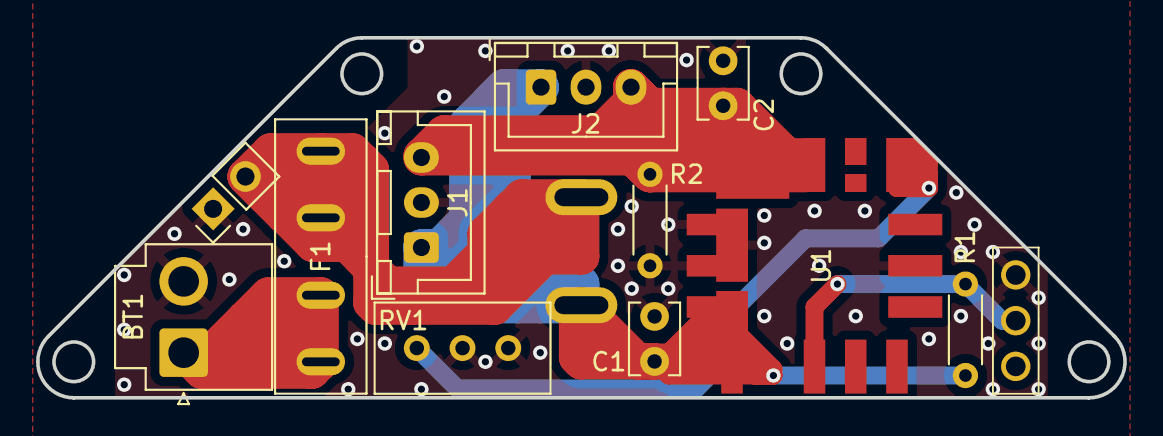
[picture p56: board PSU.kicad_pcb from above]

Board: 2 copper layers, 60.4 x 20.0 mm, 13 parts (1 on the bottom side), 7 nets.

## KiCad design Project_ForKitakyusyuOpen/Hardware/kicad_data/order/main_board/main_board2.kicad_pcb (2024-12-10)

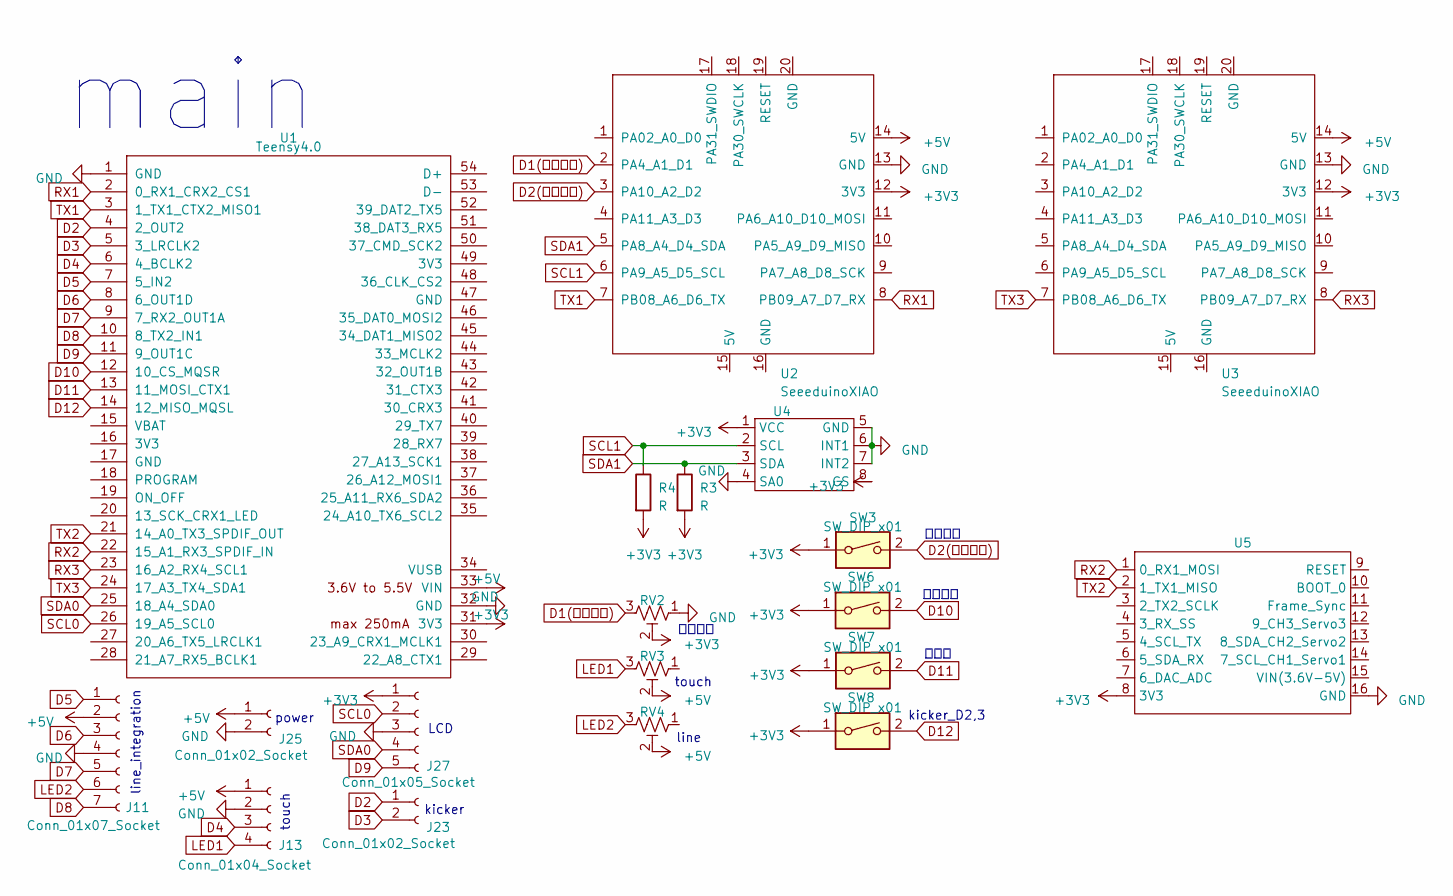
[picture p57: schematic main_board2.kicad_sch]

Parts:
J11: Conn_01x07_Socket; JST_XH_B7B-XH-A_1x07_P2.50mm_Vertical
J13: Conn_01x04_Socket; JST_XH_B4B-XH-A_1x04_P2.50mm_Vertical
J23, J25: Conn_01x02_Socket; JST_XH_B2B-XH-A_1x02_P2.50mm_Vertical
J27: Conn_01x05_Socket; JST_XH_B5B-XH-A_1x05_P2.50mm_Vertical
R3, R4: R; R_Axial_DIN0204_L3.6mm_D1.6mm_P5.08mm_Horizontal
RV2, RV3, RV4: R_Potentiometer_Trim_US; 可変抵抗
SW3, SW6, SW7, SW8: SW_DIP_x01; SW_PUSH_6mm_H7.3mm
U1: Teensy4.0; teensy 4.0
U2, U3: SeeeduinoXIAO; seeeduinoXIAO
U4: L3GD20H_Module
U5: OpenMV

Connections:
+3V3: J27.1, R3.2, R4.2, RV2.2, SW3.1, SW6.1, SW7.1, SW8.1, U1.31 (3V3), U2.12 (3V3), U3.12 (3V3), U4.1 (VCC), U4.8 (CS), U5.8 (3V3)
+5V: J11.2, J13.1, J25.1, RV3.2, RV4.2, U1.33 (VIN), U2.14 (5V), U3.14 (5V)
D1(ジャイロ): RV2.3, U2.2 (PA4_A1_D1)
D2: J23.1, U1.4 (2_OUT2)
D2(ジャイロ): SW3.2, U2.3 (PA10_A2_D2)
D3: J23.2, U1.5 (3_LRCLK2)
D4: J13.3, U1.6 (4_BCLK2)
D5: J11.1, U1.7 (5_IN2)
D6: J11.3, U1.8 (6_OUT1D)
D7: J11.5, U1.9 (7_RX2_OUT1A)
D8: J11.7, U1.10 (8_TX2_IN1)
D9: J27.5, U1.11 (9_OUT1C)
D10: SW6.2, U1.12 (10_CS_MQSR)
D11: SW7.2, U1.13 (11_MOSI_CTX1)
D12: SW8.2, U1.14 (12_MISO_MQSL)
GND: J11.4, J13.2, J25.2, J27.3, RV2.1, U1.1 (GND), U1.32 (GND), U2.13 (GND), U3.13 (GND), U4.4 (SA0), U4.5 (GND), U4.6 (INT1), U4.7 (INT2), U5.16 (GND)
LED1: J13.4, RV3.3
LED2: J11.6, RV4.3
RX1: U1.2 (0_RX1_CRX2_CS1), U2.8 (PB09_A7_D7_RX)
RX2: U1.22 (15_A1_RX3_SPDIF_IN), U5.1 (0_RX1_MOSI)
RX3: U1.23 (16_A2_RX4_SCL1), U3.8 (PB09_A7_D7_RX)
SCL0: J27.2, U1.26 (19_A5_SCL0)
SCL1: R4.1, U2.6 (PA9_A5_D5_SCL), U4.2 (SCL)
SDA0: J27.4, U1.25 (18_A4_SDA0)
SDA1: R3.1, U2.5 (PA8_A4_D4_SDA), U4.3 (SDA)
TX1: U1.3 (1_TX1_CTX2_MISO1), U2.7 (PB08_A6_D6_TX)
TX2: U1.21 (14_A0_TX3_SPDIF_OUT), U5.2 (1_TX1_MISO)
TX3: U1.24 (17_A3_TX4_SDA1), U3.7 (PB08_A6_D6_TX)

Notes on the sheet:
line_integration
リセット
ジャイロ
LCD
power
main
カメラ
touch
line
kicker
kicker_D2,3

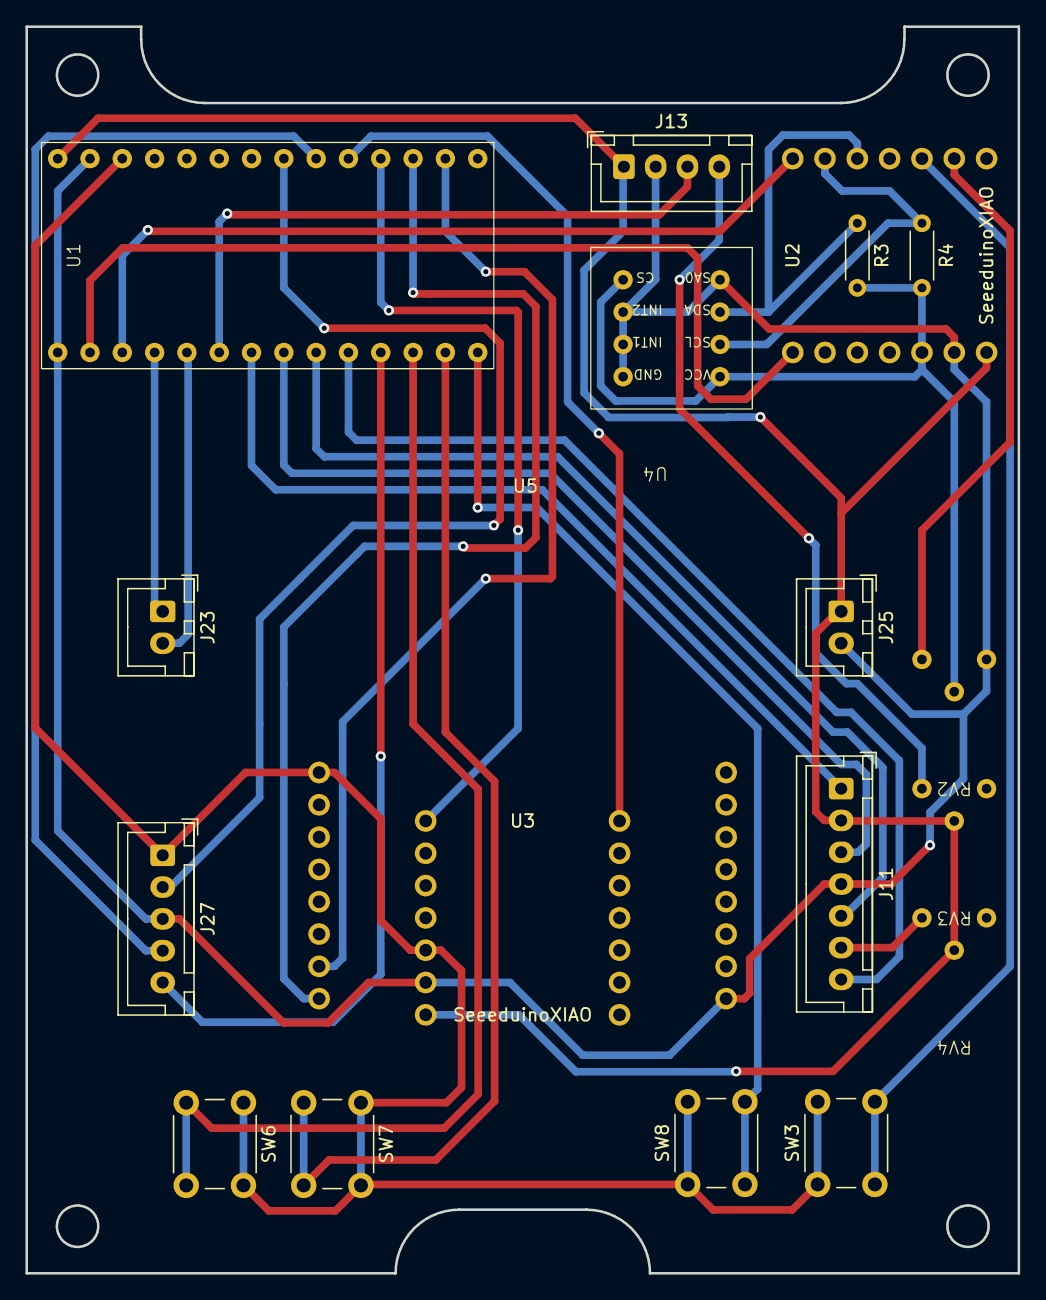
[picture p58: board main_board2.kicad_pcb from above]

Board: 2 copper layers, 78.0 x 98.0 mm, 19 parts (0 on the bottom side), 28 nets.

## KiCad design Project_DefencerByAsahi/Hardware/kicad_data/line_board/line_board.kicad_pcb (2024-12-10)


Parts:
C1, C2, C3, C4, C5, C6, C7, C8, C9, C10, C11, C12, C13, C14, C15, C16: C_Small; C_Disc_D3.8mm_W2.6mm_P2.50mm
C17: C; CP_Radial_D5.0mm_P2.50mm
D1, D2, D3, D4, D5, D6, D7, D8, D9, D10, D11, D12, D13, D14, D15, D16: LED; LED_D3.0mm_Clear
J1: Conn_01x05_Female; JST_XH_B5B-XH-A_1x05_P2.50mm_Vertical
U1, U2, U3, U4, U5, U6, U7, U8, U9, U10, U11, U12, U13, U14, U15, U16: Line_sennsor; Line_Sensor
U17: SeeeduinoXIAO; seeeduinoXIAO

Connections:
+3.3V: C1.1, C2.1, C3.1, C4.1, C5.1, C6.1, C7.1, C8.1, C9.1, C10.1, C11.1, C12.1, C13.1, C14.1, C15.1, C16.1, U1.2 (VCC), U2.2 (VCC), U3.2 (VCC), U4.2 (VCC), U5.2 (VCC), U6.2 (VCC), U7.2 (VCC), U8.2 (VCC), U9.2 (VCC), U10.2 (VCC), U11.2 (VCC), U12.2 (VCC), U13.2 (VCC), U14.2 (VCC), U15.2 (VCC), U16.2 (VCC), U17.12 (3V3)
+5V: J1.1, U17.14 (5V)
D0: U1.3 (VOUT), U2.3 (VOUT), U17.1 (PA02_A0_D0)
D1: U3.3 (VOUT), U4.3 (VOUT), U17.2 (PA4_A1_D1)
D2: U5.3 (VOUT), U6.3 (VOUT), U17.3 (PA10_A2_D2)
D3: U7.3 (VOUT), U8.3 (VOUT), U17.4 (PA11_A3_D3)
D4: U9.3 (VOUT), U10.3 (VOUT), U17.5 (PA8_A4_D4_SDA)
D5: U11.3 (VOUT), U12.3 (VOUT), U17.6 (PA9_A5_D5_SCL)
D6: U13.3 (VOUT), U14.3 (VOUT), U17.9 (PA7_A8_D8_SCK)
D7: U15.3 (VOUT), U16.3 (VOUT), U17.10 (PA5_A9_D9_MISO)
GND: C1.2, C2.2, C3.2, C4.2, C5.2, C6.2, C7.2, C8.2, C9.2, C10.2, C11.2, C12.2, C13.2, C14.2, C15.2, C16.2, C17.1, J1.2, U1.4 (GND), U2.4 (GND), U3.4 (GND), U4.4 (GND), U5.4 (GND), U6.4 (GND), U7.4 (GND), U8.4 (GND), U9.4 (GND), U10.4 (GND), U11.4 (GND), U12.4 (GND), U13.4 (GND), U14.4 (GND), U15.4 (GND), U16.4 (GND), U17.13 (GND)
unnamed: D1.1 (K), U1.1 (K(-))
unnamed: D2.1 (K), U2.1 (K(-))
unnamed: D3.1 (K), U3.1 (K(-))
unnamed: D4.1 (K), U4.1 (K(-))
unnamed: D5.1 (K), U5.1 (K(-))
unnamed: D6.1 (K), U6.1 (K(-))
unnamed: D7.1 (K), U7.1 (K(-))
unnamed: D8.1 (K), U8.1 (K(-))
unnamed: D9.1 (K), U9.1 (K(-))
unnamed: D10.1 (K), U10.1 (K(-))
unnamed: D11.1 (K), U11.1 (K(-))
unnamed: D12.1 (K), U12.1 (K(-))
unnamed: D13.1 (K), U13.1 (K(-))
unnamed: D14.1 (K), U14.1 (K(-))
unnamed: D15.1 (K), U15.1 (K(-))
unnamed: D16.1 (K), U16.1 (K(-))
R-Trim: C17.2, D1.2 (A), D2.2 (A), D3.2 (A), D4.2 (A), D5.2 (A), D6.2 (A), D7.2 (A), D8.2 (A), D9.2 (A), D10.2 (A), D11.2 (A), D12.2 (A), D13.2 (A), D14.2 (A), D15.2 (A), D16.2 (A), J1.3
RX: J1.5, U17.8 (PB09_A7_D7_RX)
TX: J1.4, U17.7 (PB08_A6_D6_TX)



Board: 2 copper layers, 98.0 x 98.0 mm, 51 parts (3 on the bottom side), 30 nets.

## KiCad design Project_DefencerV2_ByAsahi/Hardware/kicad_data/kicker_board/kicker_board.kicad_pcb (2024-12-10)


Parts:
C1: C; CP_Radial_D22.0mm_P10.00mm_SnapIn
D1: D_Filled; D_DO-15_P10.16mm_Horizontal
J1, J4, J15: Conn_01x03_Female; PinHeader_1x03_P2.54mm_Vertical
J2, J3, J5, J6, J7, J8, J9, J10, J11, J12, J13, J14: Conn_01x02_Female; PinHeader_1x02_P2.54mm_Vertical
J16: Conn_01x01_Female; PinHeader_1x01_P2.54mm_Vertical
Q1: Q_PMOS_GDS; Pch MOSFET
Q2, Q4: Q_NMOS_GDS; Nch MOSFET
Q3: Q_PMOS_GDS; Nch MOSFET
Q5: Q_NMOS_GDS; Pch MOSFET
R1, R2, R3, R4, R5, R6, R7, R8: R; R_Axial_DIN0207_L6.3mm_D2.5mm_P7.62mm_Horizontal
R9: R; R_Axial_Power_L20.0mm_W6.4mm_P5.08mm_Vertical
U1: XL6009

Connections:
5V: Q3.2 (D), R5.1
+5V: J1.2, J9.1, J10.1, J11.1, J14.1, Q3.3 (S), R4.1
+12V: J5.1, J6.1, J7.1, J13.1, U1.1 (IN+)
+48V: Q1.3 (S), R1.1, U1.3 (OUT+)
GND: C1.2, J1.1, J5.2, J6.2, J7.2, J8.1, J9.2, J10.2, J11.2, J12.1, J13.2, J14.2, Q2.3 (S), Q4.3 (S), R2.1, R6.2, R7.1, R9.1, U1.2 (IN-), U1.4 (OUT-)
unnamed: C1.1, D1.1 (K), J3.1, J8.2, J12.2, Q1.2 (D)
unnamed: D1.2 (A), J3.2, Q5.2 (D)
unnamed: J1.3, J16.1
unnamed: J4.1, J15.1
unnamed: J4.2, J15.2
unnamed: J4.3, J15.3
unnamed: Q1.1 (G), Q2.2 (D), R1.2
unnamed: Q2.1 (G), R2.2, R3.2
unnamed: Q3.1 (G), Q4.2 (D), R4.2
unnamed: Q4.1 (G), R7.2, R8.2
unnamed: Q5.1 (G), R5.2, R6.1
unnamed: Q5.3 (S), R9.2
digital1: J2.1, R3.1
digital2: J2.2, R8.1

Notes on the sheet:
10k
100


Board: 2 copper layers, 110.0 x 77.5 mm, 33 parts (0 on the bottom side), 19 nets.

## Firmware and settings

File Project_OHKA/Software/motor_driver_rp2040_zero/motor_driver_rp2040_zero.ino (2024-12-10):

#include <Arduino.h>
#include <Adafruit_NeoPixel.h>

const int PIN_MOTOR_INA[4] = {D2, D5,  D8, D26};
const int PIN_MOTOR_INB[4] = {D4, D7, D14, D27};
const int PIN_MOTOR_PWM[4] = {D3, D6, D15, D28};

#define DIN_PIN 16            // NeoPixel　の出力ピン番号はGP16
#define LED_COUNT 1           // LEDの連結数
#define WAIT_MS 1000          // 次の点灯までのウエイト
#define BRIGHTNESS 32        // 輝度
Adafruit_NeoPixel pixels(LED_COUNT, DIN_PIN, NEO_GRB + NEO_KHZ800);

class Motor{
private:
  int _rotate;
  int _power;

public:
  /// @brief モーターデータをセットします。
  /// @param power モーター駆動パワー(0~100%)
  /// @param rotate モーター回転方向(0:順転, 1:逆転)
  void set(int power, int rotate)
  {
    this->_power = power;
    this->_rotate = rotate;
  }
  
  /// @brief モーター駆動パワーを取得します。
  /// @return モーター駆動パワー(0-100%)
  int get_power()
  {
    return this->_power;
  }

  /// @brief モーター回転方向を取得します。
  /// @return モーター回転方向(0:順転, 1:逆転)
  int get_rotate()
  {
    return this->_rotate;
  }
};

Motor motors[4];

void get_motor_data()
{
  String data = "aaa";

  if(Serial1.available() > 0)
  {
    data = Serial1.readStringUntil('\n');
    Serial.println(data);

    pixels.clear();
    pixels.setPixelColor(0, pixels.Color(0, 0, BRIGHTNESS));
    pixels.show();
  }
  else
  {
    pixels.clear();
    pixels.setPixelColor(0, pixels.Color(0, 0, 0));
    pixels.show();
  }

  if(data[0] != 'a')
  {
    int motora_rotate = ( (String)data[0]).toInt();    int motorb_rotate = ( (String)data[4]).toInt();
    int motorc_rotate = ( (String)data[8]).toInt();
    int motord_rotate = ( (String)data[12]).toInt();

    int motora_power = (((String)data[1] + (String)data[2] + (String)data[3])).toInt();
    int motorb_power = (((String)data[5] + (String)data[6] + (String)data[7])).toInt();
    int motorc_power = (((String)data[9] + (String)data[10] + (String)data[11])).toInt();
    int motord_power = (((String)data[13] + (String)data[14] + (String)data[15])).toInt();

    motors[0].set(motora_power, motora_rotate);
    motors[1].set(motorb_power, motorb_rotate);
    motors[2].set(motorc_power, motorc_rotate);
    motors[3].set(motord_power, motord_rotate);
  }
}

void setup() {
  analogWriteFreq(20000);
  analogWriteRange(1023);

  pixels.begin();             //NeoPixel制御開始

  for(int i = 0; i < 4; i++) {
    motors[i].set(0, 0);

    pinMode(PIN_MOTOR_INA[i], OUTPUT);
    pinMode(PIN_MOTOR_INB[i], OUTPUT);
  }

  pixels.clear();
  pixels.setPixelColor(0, pixels.Color(0, 0, 0));
  pixels.show();

  Serial.begin(9600);

  Serial1.setTX(D0);
  Serial1.setRX(D1);
  Serial1.begin(115200);
  Serial1.setTimeout(10);
}

void loop() {
  get_motor_data();

  //4つのモーターに対して処理
  for(int i = 0; i < 4; i++)
  {
    if(motors[i].get_rotate() == 0)
    {
      if(motors[i].get_power() == 0)
      {
        digitalWrite(PIN_MOTOR_INA[i], LOW);
        digitalWrite(PIN_MOTOR_INB[i], LOW);
        analogWrite(PIN_MOTOR_PWM[i], 0);
      }
      else
      {
        digitalWrite(PIN_MOTOR_INA[i], HIGH);
        digitalWrite(PIN_MOTOR_INB[i], LOW);
        analogWrite(PIN_MOTOR_PWM[i], (int)((motors[i].get_power()) / 100.0 * 1023.0));
      }
    }
    else
    {
      if(motors[i].get_power() == 0)
      {
        digitalWrite(PIN_MOTOR_INA[i], HIGH);
        digitalWrite(PIN_MOTOR_INB[i], HIGH);
        analogWrite(PIN_MOTOR_PWM[i], 0);
      }
      else
      {
        digitalWrite(PIN_MOTOR_INA[i], LOW);
        digitalWrite(PIN_MOTOR_INB[i], HIGH);
        analogWrite(PIN_MOTOR_PWM[i], (int)((motors[i].get_power()) / 100.0 * 1023.0));
      }
    }
  }
}

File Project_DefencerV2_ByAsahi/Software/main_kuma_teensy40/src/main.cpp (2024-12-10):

#include <Arduino.h>

#include <Adafruit_GFX.h>
#include <Adafruit_SSD1306.h>

#define SCREEN_WIDTH 128 // OLED display width, in pixels
#define SCREEN_HEIGHT 64 // OLED display height, in pixels
#define OLED_RESET     -1 // Reset pin # (or -1 if sharing Arduino reset pin)
#define SCREEN_ADDRESS 0x3C ///< See datasheet for Address; 0x3D for 128x64, 0x3C for 128x32

Adafruit_SSD1306 display(SCREEN_WIDTH, SCREEN_HEIGHT, &Wire, OLED_RESET);

#include "DSR1202.h"


#include "timer.hpp"
#include "button.hpp"

#include "serial_receive.hpp"
#include "motor.hpp"
#include "engelline.hpp"


#define ROBO_SPEED 50
#define court_half_Y 109
#define court_half_B 121
#define goal_near_Y 64 //前に出るゴールとの距離（黄色）
#define goal_near_B 80 //　　　　　　　　　　　（青色）
#define goal_kado_Y 104 //ラインの端っこの距離（黄色）
#define goal_kado_B 64 //                   （青色）
#define goal_kado_Y_R 33
#define goal_kado_Y_L 33

Button btEnter(30, Button_Type::BUTTON_PULLUP);
Button btLeft(31, Button_Type::BUTTON_PULLUP);
Button btRight(32, Button_Type::BUTTON_PULLUP);

Timer Line_Timer;
Timer InLine_Timer;
Timer AfterLine_Wait;
Timer Ball_timer;

Timer LineTrace_FakeTimer;

int Line_Deg_First;
int LineDegBefore;
bool bLine_Detected;
bool bIsLineHalfOut;
double move_deg;
double move_speed;
int cam_date[2];
int goal_near;
int goal_kado_R;
int goal_kado_L;
int old_gyro; 
int old_line;
bool line;


bool yellow = 0;
bool isLineTrace;

bool Line_Moving;

bool start_program = false;

// now_mode : 現在のロボットの状態を表す
// 0 : ライントレース
// 1 : ボール追跡
// 2 : ゴール帰着
int now_mode = 0;

bool is_running = false;

void setup() {
  pinMode(30, INPUT_PULLDOWN);
  pinMode(31, INPUT_PULLDOWN);
  pinMode(32, INPUT_PULLDOWN);

  serials_init();
  motor_init();

  display.begin(SSD1306_SWITCHCAPVCC, SCREEN_ADDRESS);
  display.setTextColor(SSD1306_WHITE);
  display.setTextWrap(false);

  Serial.begin(9600);
}

void loop() {
  serials_receive();

  btEnter.loop();
  btLeft.loop();
  btRight.loop();

  Line_Timer.tick();
  AfterLine_Wait.tick();
  InLine_Timer.tick();
  Ball_timer.tick();
  LineTrace_FakeTimer.tick();
  pid_motion.pid_gyro();


  if(btLeft.isPushed())
  {
    yellow = !yellow;
  }

  if(btEnter.isPushed())
  {
    start_program = !start_program;
  }

  if(yellow == 0)
  {    
      
    cam_date[0] = Cam_GoalY_Deg; 
    cam_date[1] = Cam_GoalY_Dis; 
    goal_near = goal_near_Y;
    goal_kado_R = goal_kado_Y_R;
    goal_kado_L = goal_kado_Y_L;
    display.setCursor(10, 10);
    display.println("yellow");
    display.display();
  }
  else
  {
    cam_date[0] = Cam_GoalB_Deg; 
    cam_date[1] = Cam_GoalB_Dis;
    goal_near = goal_near_B;
    //goal_kado = goal_kado_B;
    display.setCursor(10, 10);
    display.println("blue");
    display.display();
  }

  
  if(Line_Deg != -1)
  {
    if(Ball_Deg != -1)
    {
      if((Ball_Deg > 350 || Ball_Deg < 10) || (Ball_Deg > 150 && Ball_Deg < 200))
      {
        move_deg = (-1, 0);
        move_deg = (degrees(move_deg));
        move_deg = move_deg * -2.0;
        move_speed = 0;
      }
      else if(Ball_Deg <= 180)
      {
        move_deg = atan2(-1, 1);
        move_deg = (degrees(move_deg));
        move_deg = move_deg * -2.0;
        move_speed = 50 + (Ball_Deg >= 90 ? (180 - Ball_Deg) / 1.5 : Ball_Deg / 1.5);
      }
      else
      {
        move_deg = atan2(-1, -1);
        move_deg = (degrees(move_deg));
        move_deg = move_deg * -2.0;
        move_speed = 50 + (Ball_Deg >= 270 ? (360 - Ball_Deg) / 1.5 : (Ball_Deg - 180) / 1.5);
      }  
    }
    else
    {
      move_deg = cam_date[0] * 2;
      move_speed = cam_date[1] / 2.0;
    }
  }
  else
  {
    if(Ball_Deg != -1)
    {
      if((Ball_Deg > 355 || Ball_Deg < 5) || (Ball_Deg > 150 && Ball_Deg < 200))
      {
        move_deg = (-1, 0);
        move_deg = (degrees(move_deg));
        move_speed = 0;
      }
      else if(Ball_Deg <= 180)
      {
        move_deg = atan2(-1, 1);
        move_deg = (degrees(move_deg));
        if(Ball_Distance > 0)
        {
          move_speed = Ball_Distance * 1.2;
        }
        move_deg = (move_deg -90) * -1;
      }
      else
      {
        move_deg = atan2(-1, -1);
        move_deg = (degrees(move_deg));
        if(Ball_Distance > 0)
        {
          move_speed = Ball_Distance * 1.2;
        }
        move_deg = (move_deg -90) * -1;

      }  
    }
    else
    {
      move_deg = cam_date[0] * 2;
      move_speed = cam_date[1] / 2.0;
    }  
  }

  if(start_program)
  {
    if(Line_Deg != -1)
    {
      old_line = Line_Deg;
    }

    if(now_mode == 0)  //ライントレースモードの時
    {   
      if(Line_Deg != -1)
      {
        if(Ball_Deg != -1)
          {
            if(cam_date[0] > 115 && cam_date[0] < 130)
            {
              if(Ball_Deg <= 180)
              {
                move(0,0);
              }
              else
              {
                move(move_deg, move_speed);
              }
            }
            else if(cam_date[0] > 39 && cam_date[0] < 81)
            {
              if(Ball_Deg <= 180)
              {
                move(move_deg, move_speed);
              }
              else
              {
                move(0, 0);
              }
            }
            else
            {
              move(move_deg, move_speed);
            }
          }
          else
          {
            if(cam_date[0] > 78 && cam_date[0] < 103)//ゴールの端から端までの角度
            {
              move(0, 0);
            }
            else
            {
              if(cam_date[1] < goal_kado_R)
              {
                if(Line_Deg <= 180)
                {
                  move(315, 55);
                }
                else
                {
                  move(45, 55);
                }
              }
              else
              {
                move(cam_date[0] * 2, cam_date[1] / 2.0);
              }
            }
          }
      }
      else
      {
        if(cam_date[1] < goal_near)
        {
            if(Ball_Deg <= 180)
            {
              move(70, 45);
            }
            else
            {
              move(290, 45);
            }       
        }
        else
        {
          if(cam_date[0] > 78 && cam_date[0] < 103)//ゴールの端から端までの角度
          {
            if(Ball_Deg <= 180)
            {
              move(110, 50);
            }
            else
            {
              move(250, 50);
            }            
          }
          else
          {
            move(cam_date[0] * 2, cam_date[1] / 2.0);
          }
        }
      }
    } 
    else if(now_mode == 1)  //ボール追跡モードの時
    {
      //ライン踏んだらコート内に戻る
      if(Line_Deg != -1)
      {
        move(Line_Deg, 50);
      }
      else
      {
        move(move_deg, 50);        
      }   
      //動く的なsomething
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

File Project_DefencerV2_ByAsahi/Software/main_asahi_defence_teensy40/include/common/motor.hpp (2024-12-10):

#ifndef _MOTOR_H
#define _MOTOR_H

#include <Arduino.h>
#include "DSR1202.h"
#include "serial_receive.hpp"

DSR1202 md = DSR1202(0);

//origin = 0.13
float P_GAIN = 0.13;
float I_GAIN = 0.2;
float D_GAIN = 0.59;

float P_GAIN_CAM = 0.7;
float D_GAIN_CAM = 2;

int deviation;
int old_deviation;

int pid_val = 0;

int now_time;
int old_time;

class PID_Motion{
private:
    int gyro_pid_goal = 512;
public:
    float p_val_g;
    float i_val_g;
    float d_val_g;
    
    int pid_gyro()
    {
        //ジャイロ角度を用いたPIDでの角度制御
        now_time = millis();
        
        float dt = (now_time - old_time) / 1000;

        p_val_g = (Gyro_Deg - gyro_pid_goal);
                
        deviation = p_val_g;
        d_val_g = deviation - old_deviation;
        old_deviation = deviation;  

        pid_val = (int)(p_val_g * P_GAIN + d_val_g * D_GAIN);

        old_time = now_time;

        return 0;
    }

    void set_pid_goal(int data)
    {
        gyro_pid_goal = data;
    }

    void set_pid_gain(int p)
    {
        P_GAIN = p;
    }

    int pid_camera(int deg)
    {
        //カメラ角度を用いたPIDでの角度制御

        int p_val = (deg >= 90 ? deg - 180 : deg) * P_GAIN_CAM;   
        int d_val = 0;

        deviation = p_val;
        d_val = (deviation - old_deviation);
        old_deviation = deviation;  

        d_val = d_val * D_GAIN_CAM;

        pid_val = p_val + d_val;

        return 0;
    }
};

PID_Motion pid_motion;

void motor_init(){
    md.Init();
    md.move(0, 0, 0, 0);
}

void motor_power(float* powers){
    md.move((int)(-powers[0]), (int)(-powers[1]), (int)(-powers[2]), (int)(-powers[3]));            
}

void motor_power(float a, float b, float c, float d){
    md.move(-a, -b, -c, -d);
}

void move(int deg, int power){
    float motor_powers[4];

    //モーターの角度による出力値計算
    motor_powers[0] = -sin(radians(deg - 50)) * power;
    motor_powers[1] = sin(radians(deg + 50)) * power;
    motor_powers[2] = -sin(radians(deg - 130)) * power;
    motor_powers[3] = sin(radians(deg + 130)) * power;

    float max_motor_power = 0;

    for(int i = 0; i < 4; i++)
    {
        if(max_motor_power < abs(motor_powers[i]))
        {
            max_motor_power = abs(motor_powers[i]);
        }
    }

    float motor_power_mul = power / max_motor_power;
    
    for(int i = 0; i < 4; i++)
    {
        motor_powers[i] = motor_powers[i] * motor_power_mul;
    }
    
    
    if(power == 0)
    {
        for(int i = 0; i < 4; i++)
        {
            motor_powers[i] = 0;
        }
    }

    int pid_fixed_val = pid_val >= (100 - max_motor_power) ? (100 - max_motor_power) : pid_val;

    motor_powers[0] = motor_powers[0] - pid_fixed_val;
    motor_powers[1] = motor_powers[1] + pid_fixed_val;
    motor_powers[2] = motor_powers[2] - pid_fixed_val;
    motor_powers[3] = motor_powers[3] + pid_fixed_val;

    for(int i = 0; i < 4; i++)
    {
        motor_powers[i] = min(max(motor_powers[i], -100), 100);
    }

    //モーター出力

    motor_power(motor_powers);
}

void motor_break()
{
    md.motor_break();
}

#endif

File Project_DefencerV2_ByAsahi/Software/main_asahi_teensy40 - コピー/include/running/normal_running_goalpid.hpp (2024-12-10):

#ifndef _NORMAL_RUNNING_GOALPID_H
#define _NORMAL_RUNNING_GOALPID_H

#include <Arduino.h>

#include "common/timer.hpp"
#include "common/motor.hpp"
#include "common/serial_receive.hpp"

int now_mode;

class Normal_Running_GoalPID
{
private:
    Timer LimitOfSideMove;
    Timer Ball_timer;

    int ROBO_SPEED = 58;
    int mode;


    float Line_SpeedPer = 0.8;
    float AfterLine_SpeedPer = 0.85;

    int Camera_Data[4];

    bool CheckDegToBeforeLine(int deg)
    {
        int check_deg = 60;
        if(engelline.Line_Deg_First + 180 + check_deg >= 360)
        {
            if(deg >= engelline.Line_Deg_First + 180 - check_deg || deg <= engelline.Line_Deg_First + 180 + check_deg - 360)
            {
                return true;
            }
            else
            {
                return false;
            }
        }
        else
        {
            if(engelline.Line_Deg_First + 180 - check_deg >= 360)
            {
                if(deg >= engelline.Line_Deg_First + 180 - check_deg - 360 && deg <= engelline.Line_Deg_First + 180 + check_deg - 360)
                {
                    return true;
                }
                else
                {
                    if(deg >= engelline.Line_Deg_First + 180 - check_deg && deg <= engelline.Line_Deg_First + 180 + check_deg)
                    {
                        return true;
                    }
                    else
                    {
                        return false;
                    }
                }
            }
        }

        return false;
    }

    void set_camera_data(int type)
    {
        if(type == 0)
        {
            Camera_Data[0] = Yellow_Goal_Deg - 2;
            Camera_Data[1] = Yellow_Goal_Distance;
            Camera_Data[2] = Blue_Goal_Deg - 2;
            Camera_Data[3] = Blue_Goal_Distance;
            mode = 1;
        }
        else if(type == 1)
        {
            Camera_Data[0] = Blue_Goal_Deg - 2;
            Camera_Data[1] = Blue_Goal_Distance;
            Camera_Data[2] = Yellow_Goal_Deg - 2;
            Camera_Data[3] = Yellow_Goal_Distance;
            mode = 2;
        }

        pid_motion.pid_gyro();
    }

public:
    int get_robo_speed()
    {
        return ROBO_SPEED;
    }

    void normal_running(int deg_type)
    {  
        int move_deg = 0;
        int move_speed = 0;

        set_camera_data(deg_type);

        engelline.engelline_main(ROBO_SPEED - 10);
        ball_tracking_gyro.ball_tracking_main(ROBO_SPEED - 7);

        //TODO: ボールの回り込みの最適化
        if(engelline.IsLineMovement())
        {
            LimitOfSideMove.stop();
            LimitOfSideMove.reset();

            move_deg = engelline.get_degrees();
            move_speed = engelline.get_speed();
        }
        else
        {        
            if(Ball_Distance >= 40)//ボールを追いかけたいボールの距離
            {
                if(ball_tracking_camera.IsAbleToTracking())
                {  
                    move_deg = ball_tracking_gyro.get_degrees();
                    move_speed = ball_tracking_gyro.get_speed();

                    if(engelline.AfterLine_Wait.get_value() <= 400 || !engelline.AfterLine_Wait.isticking())
                    {
                        move_speed = ROBO_SPEED * AfterLine_SpeedPer;
                    }

                    if(abs(sin(radians(move_deg))) >= abs(sin(radians(45))))
                    {
                        LimitOfSideMove.start();
                        if(LimitOfSideMove.get_value() >= 500)
                        {
                            if(LimitOfSideMove.get_value() >= 2500)
                            {
                                LimitOfSideMove.stop();
                                LimitOfSideMove.reset();
                            }
                            else
                            {
                                if(Ball_Distance <= 85)
                                {
                                    move_speed = move_speed * 0.85;
                                }
                            }
                        }
                    }
                    else
                    {
                        LimitOfSideMove.stop();
                        LimitOfSideMove.reset();
                    }
                }
            }
            else
            {
                if(mode == 1)//黄ゴール守りの時
                {
                    if(Yellow_Goal_Deg == 255)//ゴールが見えているか
                    {
                        move_deg = 180;
                        move_speed = 40;
                    }
                    else if(Ball_Distance > 43)//コートの半分
                    {
                        move_deg = move_deg;
                        move_speed = move_speed;
                    }
                    else
                    {
                        if(Ball_Deg == -1)
                        {
                            move_deg = Yellow_Goal_Deg * 2;
                            move_speed = min(Yellow_Goal_Distance / 2, 40);
                        }
                        else if(Yellow_Goal_Distance < 102)//止まってほしい位置
                        {
                            move_deg = 0;
                            move_speed = 0;
                            
                        }
                        else
                        {
                            move_deg = Yellow_Goal_Deg * 2;
                            move_speed = min(Yellow_Goal_Distance / 2, 40);
                        }
                    }
                }
                else if(mode == 2)//青ゴール守りの時
                {
                    if(Blue_Goal_Deg == 255)//ゴールが見えているか
                    {
                        move_deg = 180;
                        move_speed = 40;
                    }
                    else if(Ball_Distance > 43)//コートの半分
                    {
                        move_deg = move_deg;
                        move_speed = move_speed;
                    }
                    else
                    {
                        if(Ball_Deg == -1)
                        {
                            move_deg = Blue_Goal_Deg * 2;
                            move_speed = min(Blue_Goal_Distance / 2, 40);
                        }
                        else if(Blue_Goal_Deg < 102)//止まってほしい位置
                        {
                            move_deg = 0;
                            move_speed = 0; 
                        }
                        else
                        {
                            move_deg = Blue_Goal_Deg * 2;
                            move_speed = min(Blue_Goal_Distance / 2, 40);
                        }
                    }
                }
            }
        }
        move(move_deg, move_speed);
    }
};
Normal_Running_GoalPID normal_running_goalpid;



#endif
